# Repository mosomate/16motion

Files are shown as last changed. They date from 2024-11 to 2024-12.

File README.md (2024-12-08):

# What is a 16Motion carriage?
Configurable, 3D printable carriage for small (up to 40 mm wide) aluminium extrusions. A 16Motion carriage consists of four 3D printed plates put together around the extrusion and some **cheap**, **easily sourceable** hardwares including 684 (4x9x4) bearings, M3 and M4 screws and nuts.
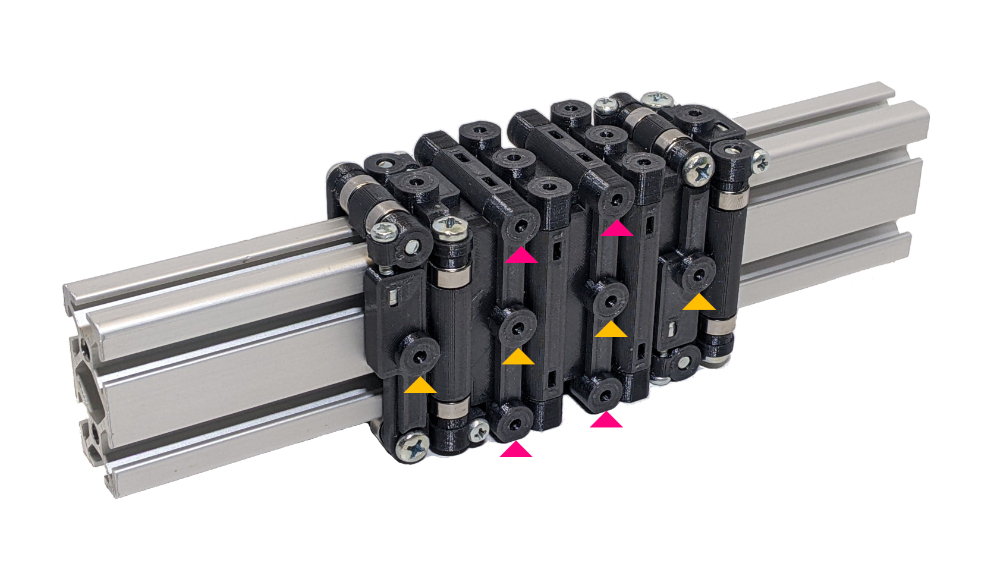
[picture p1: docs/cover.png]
16Motion main cover

Each plate has eight attachment points to mount tools and accessories to the carriage using M3 screws and nuts. These eight points split up to two groups: four **plate attachment point**s (indicated by yellow arrows) and four **carriage attachment point**s (indicated by violet arrows).

**Carriage attachment points** go through at least two plates, therefore they give additional stuctural rigidity to the carriage. If you use only **plate attachment points**, it is recommended to put an M3x16 screw into a few of the **carriage attachment points** as well.
Horizontal distance between the points is fixed at 23 mm and the vertical can be calculated with this formula: *vertical_distance = (extrusion_width + 9 mm) / 2*
# Disclaimer
**I'm not a professional mechanical engineer and haven't tested this design in a professional manner. I don't take any responsibilities for injuries and/or any damage caused by this design. Print and use it at you own risk!**

As steel bearings are rolling on aluminium, they might leave marks and/or wear out the extrusion over time. For **casual** usage it's not significant, but for **regular** usage you should consider using lubrication (e.g. a thin layer of lithium grease should do the job).

If you can accept these conditions, then have fun building your carriages!
# BOM for one plate
For one of the four plates you need:
- 3D printed plate **x1**
- 3D printer bearing spacer **x4**
- M4x(width of extrusion + 10 mm) screw **x2** *(e.g. if the extrusion is 20 mm width, screw length will be 20 mm + 10 mm = 30 mm)*
- M3x16 screw **x2**
- M3 self-locking nut **x2**
- 684 bearing **x4**
# 3D printing tips
I uploaded precompiled STLs to Thingiverse for **20 mm**, **25 mm** and **40 mm** wide extrusions. Check them out [HERE](https://www.thingiverse.com/thing:6853255). If you can't find the suitable sizes to satisfy your needs, then proceed with the customization.

A few tips I picked up during development:
- The recommended material is **PETG**
- The plates require only *touching buildplate* kind of supports
- 1 mm wall thickness and 0.5 mm top and bottom thickness worked fine for me
# Customization and assembly
You can find here the necessary steps for customizing the plates and assembling the carriage. Each step has a video tutorial at the end of it, don't forget to watch them on YouTube!
## Plate customization
- Open **FreeCAD** and open **Plate.FCStd**
- If you see nothing but the model of a ring (spacer) you have to toggle the visibility of the plate. Right click on **Plate** object and select **Appearance...**. Then open the dropdown at **Document window** and select **Flat Lines** again
- Right click on the **Plate** document and check **Skip recomputes**
- Click on **Spreadsheet** and edit the **Ideal extrusion width** and **Actual extrusion width** parameters. **Ideal extrusion width** is the theoretical width of one side of the extrusion (e.g. 20 mm) and the **Actual extrusion width** is the measured size of it (e.g. 19.9 mm)
- Right click on **Spreadsheet** and select **Recompute object**
- Recompute all remaining objects as well (Plate, Spacer and Assets)
- Select **Mesh** from the Workbench selector
- Select **Plate** object by clicking on it and click on **Create mesh from shape...** button. My preferred settings for mesh creation are: **Surface deviation => 0.1 mm** and **Angular deviation => 5.00 ˚**
- Create mesh from the **Spacer** object as well
- Export meshes by right click on them and select **Export mesh...**

Plate customization video (https://www.youtube.com/watch?v=9Bi0MCfb9tI "Plate customization | 16Motion Video Series")
## Plate assembly
- After 3D printing, drill an M4 thread into the **bottom left** and **top right** holes
- Insert an **M3 self locking nut** into the socket below one of the preload levers
- Insert an **M3x16** screw through the preload lever and drive it until it barely touches the lever
- Repeat the step above for the other lever

Plate assembly video (https://www.youtube.com/watch?v=31CdhINwxhE "Plate assembly | 16Motion Video Series")
## Carriage assembly
After you got your four plates printed and assembled, proceed with assemling the carriage. Additinal materials:
- 16 pcs of 3D printed spacers
- 16 pcs of 684 bearings
- 8 pcs of M4 screws with the length discussed in **BOM for one plate** section

Assembly:
- Put together the four plates. For this step it's nice to have long M3 screws or Allen wrenches poked through carriage attachment points
- Screw in one M4 screw into the threaded hole of a plate until it reaches the other side of the plate
- Put a spacer and a bearing in the route of the M4 screw
- Drive the screw until it can hold the spacer and the bearing
- Put an other pair of spacer and bearing in the route of the M4 screw and drive it all the way in
- Tighten the M4 screw firmly
- Repeat these steps for the remaining seven positions around the carriage
- Remove the things you used to hold the plates together

Carriage assembly video (https://www.youtube.com/watch?v=4gjbtIjSXgw "Carriage assembly | 16Motion Video Series")
## Preload settings
Here comes the tricky part. One rule: *No play, no too much tension!* Try to pay attention for having roughly the same tension for a pair of preload levers as you can see here:

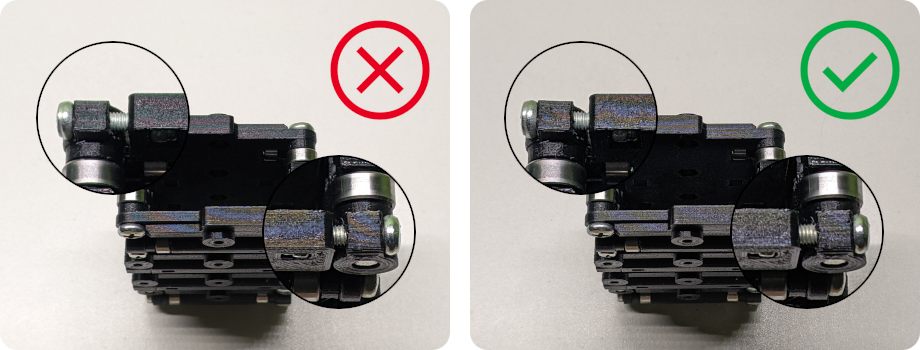
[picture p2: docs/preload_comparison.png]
Preload comparison


My best practice to set the correct amount of preload:
- Get a piece of the extrusion the carriage was made for
- Sand down the edges on one end of the extrusion
- Slide the carriage onto the extrusion and place the extrusion on a flat surface vertically
- Start tightening the screws of one pair of the preload levers in small increments
- Check if you can feel any resistance when sliding off and on the carriage again
- Stop tightening the screws if you can feel a slight resistance when sliding the carriage onto the extrusion
- Repeat this process for the rest of the preload levers

Important notes: 
- The carriage should fall through the extrusion by it's own weight when stands vertically. If it's stuck, you applied too much preload!
- It's completely normal if a few of the bearings are not rolling when the carriage is moving
- I hope the video describes the process well 

Preload settings video (https://www.youtube.com/watch?v=hf6m5ihSEW8 "Preload settings | 16Motion Video Series")
# License
Shield: [][cc-by-nc]

This work is licensed under a
[Creative Commons Attribution-NonCommercial 4.0 International License][cc-by-nc].

[][cc-by-nc]

[cc-by-nc]: https://creativecommons.org/licenses/by-nc/4.0/
[cc-by-nc-image]: https://licensebuttons.net/l/by-nc/4.0/88x31.png
[cc-by-nc-shield]: https://img.shields.io/badge/License-CC%20BY--NC%204.0-lightgrey.svg

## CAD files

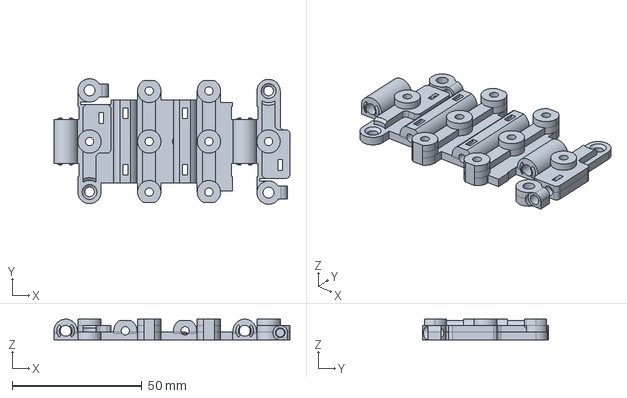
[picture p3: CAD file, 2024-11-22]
Plate.FCStd
91.0 x 48.4 x 8.00 mm
Plate
Spacer

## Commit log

2024-05-19 "Ideal" and "real" extrusion width options
    [Plate.FCStd]
2024-06-05 Wider bearing pads
    [Bearing_spacer.FCStd, Plate.FCStd]
2024-06-05 Refined adjust hinges
    [Plate.FCStd]
2024-06-06 Refined adjust pad and bearing screw pads
    [Plate.FCStd]
2024-06-08 Small tunings
    [Plate.FCStd]
2024-10-05 Simplified plate structure
    [Plate.FCStd]
2024-10-13 M4 nuts omitted
    [Plate.FCStd]
2024-10-18 Enlarged tension screw tunnels
    [Bearing_spacer.FCStd, Plate.FCStd]
2024-10-23 Fixed 3D printing compensation issue
    [Plate.FCStd]
2024-11-22 Cleaned up for FreeCAD 1.0
    [Bearing_spacer.FCStd, Plate.FCStd]
2024-12-01 Plate customization block in README
2024-12-01 Plate assembly for README
2024-12-04 Carriage assembly section in README
2024-12-08 Updated printing tips
